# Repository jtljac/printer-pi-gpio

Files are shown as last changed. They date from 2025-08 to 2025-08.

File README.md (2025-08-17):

A simple break-out board for a Raspberry Pi that makes accessing some GPIO interfaces easier for [klipper](https://www.klipper3d.org/).

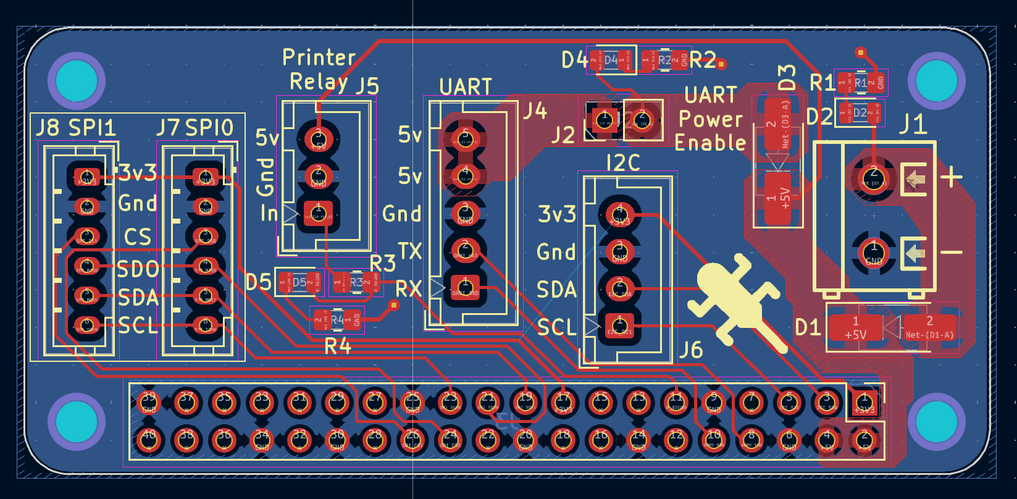
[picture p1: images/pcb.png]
The PCB


## Features
5V Power in via screw terminal for powering Pi.

UART Bus for connecting klipper directly to a control board via serial.  
The UART bus also has 2 pins for 5V, which depending on your control board can power the Pi (In my case, the [SKR-Pico](https://github.com/bigtreetech/SKR-Pico) supports this). This can be enabled using the `UART Power Enable` jumper.

Reverse current protection on both power inputs, also doubling as Power Or-ing, allowing both power inputs to be powered simultaniously safely.

LED indicators on each power input to indicate when each one is powered.

SPI bus split into 2 connectors with different CS pins (`spi0: GPIO8`, `spi1: GPIO7`), for screens and ADXLs.

I2C bus for miscellaneous purposes.

A header for connecting to a Relay Module to toggle power to the actual printer, uses `GPIO17`.  
Also features an LED to indicate when the relay is toggled.

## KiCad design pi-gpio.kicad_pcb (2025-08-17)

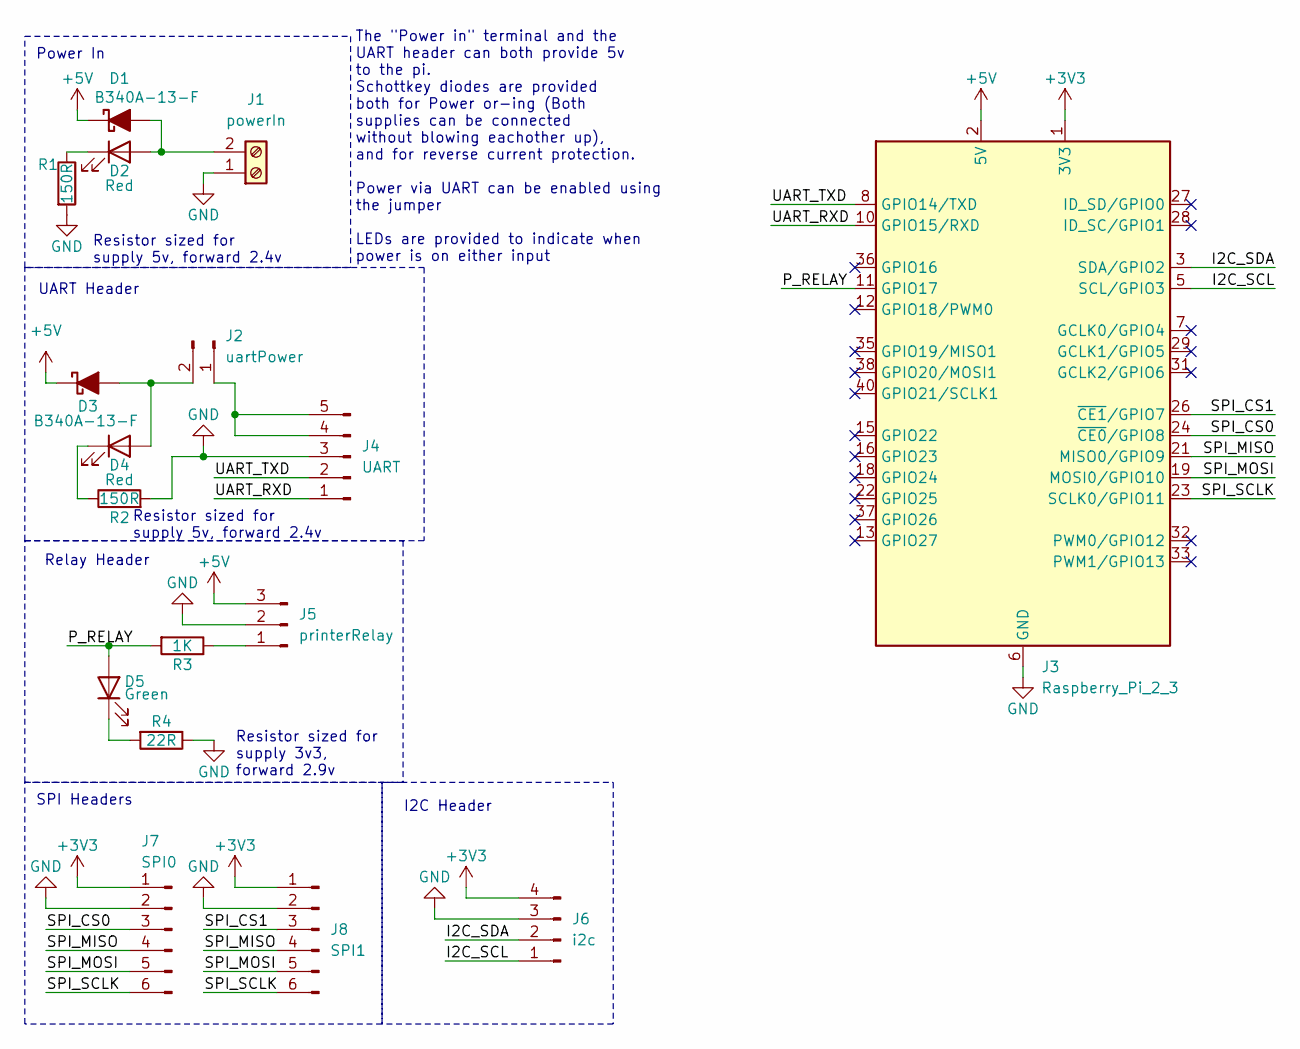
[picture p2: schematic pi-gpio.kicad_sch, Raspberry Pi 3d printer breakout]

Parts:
D1, D3: B340A-13-F; D_SMA_Handsoldering
D2, D4: Red; LED_0805_2012Metric
D5: Green; LED_0805_2012Metric
J1: powerIn; TerminalBlock_MAX_MX127-5.0-02P_1x02_P5.00mm
J2: uartPower; PinHeader_1x02_P2.54mm_Vertical
J3: Raspberry_Pi_2_3; RaspberryPi_Zero_BoardLayout
J4: UART; JST_XH_B5B-XH-A_1x05_P2.50mm_Vertical
J5: printerRelay; JST_XH_B3B-XH-A_1x03_P2.50mm_Vertical
J6: i2c; JST_XH_B4B-XH-A_1x04_P2.50mm_Vertical
J7: SPI0; JST_PH_B6B-PH-K_1x06_P2.00mm_Vertical
J8: SPI1; JST_PH_B6B-PH-K_1x06_P2.00mm_Vertical
R1, R2: 150R; R_0805_2012Metric_Pad1.20x1.40mm_HandSolder
R3: 1K; R_0805_2012Metric_Pad1.20x1.40mm_HandSolder
R4: 22R; R_0805_2012Metric_Pad1.20x1.40mm_HandSolder

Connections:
+3V3: J3.1 (3V3), J3.17 (3V3), J6.4, J7.1, J8.1
+5V: D1.1 (K), D3.1 (K), J3.2 (5V), J3.4 (5V), J5.3
/I2C_SCL: J3.5 (SCL/GPIO3), J6.1
/I2C_SDA: J3.3 (SDA/GPIO2), J6.2
/P_RELAY: D5.2 (A), J3.11 (GPIO17), R3.2
/SPI_CS0: J3.24 (~CE0/GPIO8), J7.3
/SPI_CS1: J3.26 (~CE1/GPIO7), J8.3
/SPI_MISO: J3.21 (MISO0/GPIO9), J7.4, J8.4
/SPI_MOSI: J3.19 (MOSI0/GPIO10), J7.5, J8.5
/SPI_SCLK: J3.23 (SCLK0/GPIO11), J7.6, J8.6
/UART_RXD: J3.10 (GPIO15/RXD), J4.1
/UART_TXD: J3.8 (GPIO14/TXD), J4.2
GND: J1.1, J3.6 (GND), J3.9 (GND), J3.14 (GND), J3.20 (GND), J3.25 (GND), J3.30 (GND), J3.34 (GND), J3.39 (GND), J4.3, J5.2, J6.3, J7.2, J8.2, R1.2, R2.2, R4.1
unnamed: D1.2 (A), D2.2 (A), J1.2
unnamed: D2.1 (K), R1.1
unnamed: D3.2 (A), D4.2 (A), J2.2
unnamed: D4.1 (K), R2.1
unnamed: D5.1 (K), R4.2
unnamed: J2.1, J4.4, J4.5
unnamed: J5.1, R3.1

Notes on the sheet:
Resistor sized for supply 5v, forward 2.4v
Relay Header
Power In
Resistor sized for supply 3v3, forward 2.9v
The "Power in" terminal and the UART header can both provide 5v to the pi. Schottkey diodes are provided both for Power or-ing (Both supplies can be connected without blowing eachother up), and for reverse current protection. Power via UART can be enabled using the jumper LEDs are provided to indic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
I2C Header
UART Header
SPI Headers

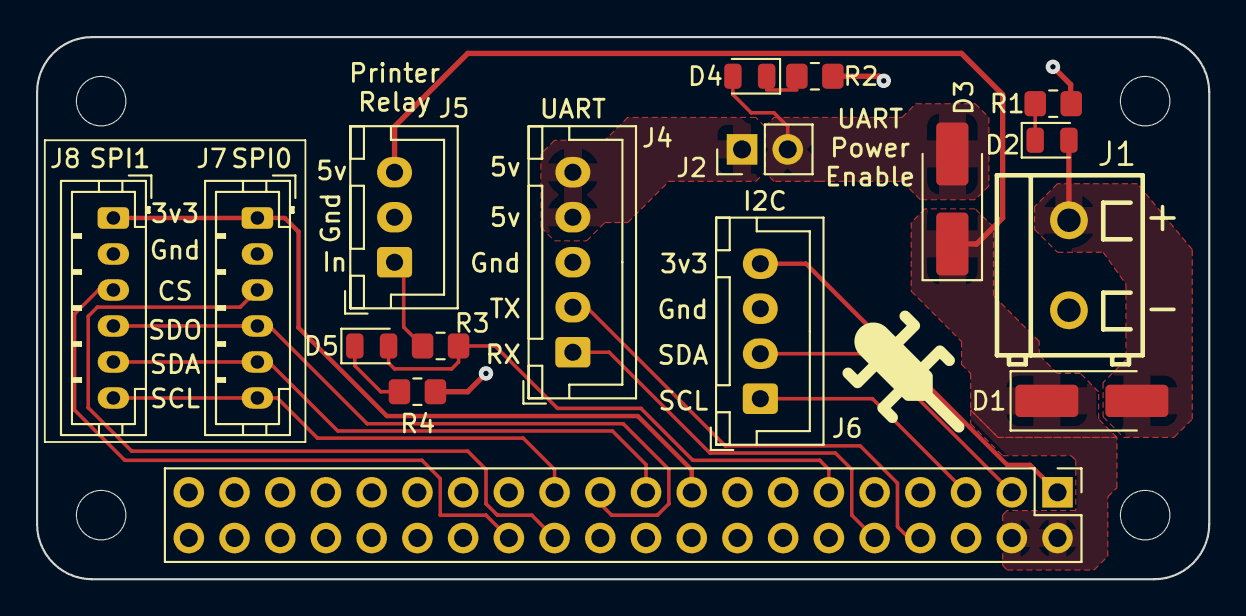
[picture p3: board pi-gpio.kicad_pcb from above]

Board: 2 copper layers, 65.1 x 30.1 mm, 17 parts (1 on the bottom side), 20 nets.

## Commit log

2025-08-17 Doubled SPI headers, added I2C
    [pi-gpio.kicad_pcb, pi-gpio.kicad_sch]
2025-08-17 Added readme
    [pi-gpio.kicad_pcb, pi-gpio.kicad_sch]
